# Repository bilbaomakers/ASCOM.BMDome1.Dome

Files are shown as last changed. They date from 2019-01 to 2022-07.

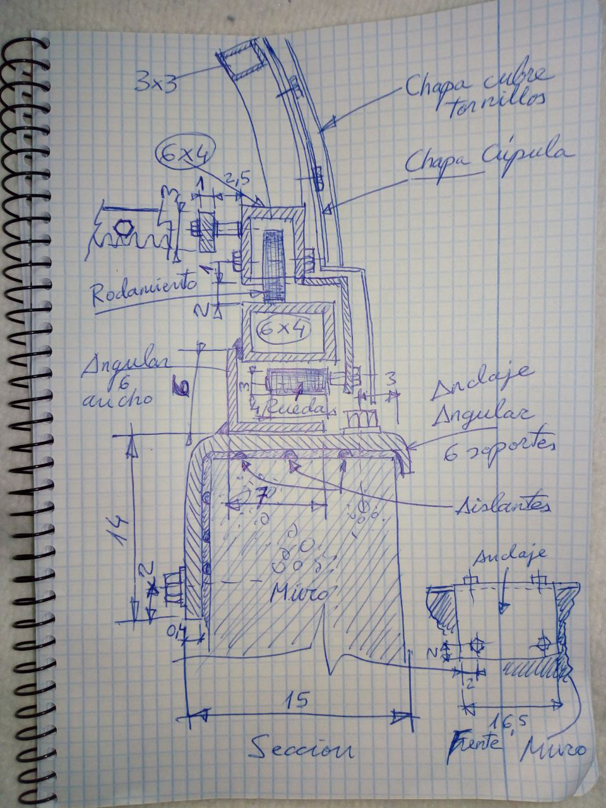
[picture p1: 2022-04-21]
DOCUMENTACION/MECANICA/IMG_20190130_000913_478.jpg

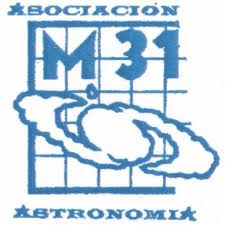
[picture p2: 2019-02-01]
DRIVER ASCOM/ASCOM.BMDome1.Dome/Resources/M31.jpg

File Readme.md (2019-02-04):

# ASCOM DOMO BILBAOMAKERS V 1.0.0

Automatizacion de la cupula del Observatorio Astronomico de Marcilla de Campos (Palencia).

Desarrollado por la comunidad Bilbaomakers: https://bilbaomakers.org/ - info@bilbaomakers.org

Desarrollado bajo licencia GNU GENERAL PUBLIC LICENSE Version 3

Descripcion:

Proyecto para desarrollar un controlador para la orientacion Azimut de la cupula del observatorio y el control de la compuerta (Shutter).

Utiliza Arduino como microcontrolador(es) y MQTT como protocolo de comunicaciones entre el PC y el Hardware

Componentes actuales:

- Driver Ascom - MQTT para el control de la cupula desde el PC (Windows) y/o fuente de tracking ( Software, Scope, ....)
- Codigo para el Hardware (Controlador Arduino para el Azimut y controlador para el Shutter).
- Diseño CAD (freecad) de los elementos mecanicos.

04/02/2019 - Proyecto en Desarrollo V 1.0.0 (Branch Development).

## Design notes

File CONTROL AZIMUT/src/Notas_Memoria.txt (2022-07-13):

NIVEL HARDWARE

Memoria interna del procesador
ROM - 448Kb para boot y core
SRAM - Static RAM - 520Kb
8Kb de SRAM en RTC (Copro)

Memoria externa ROM - SPI Flash (Antigua EEPROM)
W25Q32: 32M-bit / 4M-byte (4,194,304)
Usada habitualmente como memoria de programa, para OTA y sistema de ficheros SPIFFS, a particionar al gusto aunque para arduino en PlatformIO hay una por defecto.

NIVEL SOFTWARE

IROM - Instrucciones en ROM(flash) - Por defecto todas las funciones se almacenan ahi (no necesario modificador en programacion)
DROM - Datos en ROM(flash) - Por defecto todas las constantes se almacenan en la flash (no modificador solo declarar como constante)
D/IRAM - Combinada de las 2 pero no he conseguido saber como definirla.

IRAM_ATTR - Instruction RAM - Instrucciones (funciones) a la RAM (ISR) - void IRAM_ATTR onTimer_stepper(){}
DRAM_ATTR - Data RAM - Datos que se van a manejar desde instrucciones en la IRAM - 

NOTA: Las variables (datos no constantes iniciados en el codigo) se almacenan en la RAM, en los espacios HEAP, STACK o STATICS(volatile). No confundir con la DRAM (espacio para datos de funciones IRAM)

__NOINIT_ATTR - Datos en la Flash que NO se inicializan en restart (permanencen tras rebote).

RTC_NOINIT_ATTR - Datos en la RTC Slow memory (unica memoria accesible por el coprocesador que hay que usar el depp sleep, y accesible despues por los procesadores normales)

DMA_ATTR - Para alojamiento de datos en RAM que utilizan los perifericos DMA (Direct Access Memory). No es obligatorio (se puede poner en el STACK) porque es RAM, pero es mas seguro si hay RAM externa

Tambien hay opcion de RAM externa que no tratamos aqui.

Vista desde el "Scope":
Heap - El computo global de la RAM accesible (en cada tipo, normal, rtc, ...). Es un espacio digamos "dinamico" en funcion de "otros usos" de la RAM.
Stack - Espacio de memoria RAM para cada "Thread". Obviamente no accesible mas que por ese thread. Puede estar localizada a su vez en la RAM normal, en la RTC .....
Estatica - Localizada en HEAP e INAMOVIBLE por el compilador maligno (reservada)

xPortGetFreeHeapSize() - Heap libre (en bytes)

Proceso de arranque:

- First Boot Stage - La CPU0 (CPU_PRO) inicializa el HW y va a su vector 0 (0x40000400)
- Se inicia el second Stage del arranque donde se comprueba las particiones y el contenido de la particion OTA para decidir si cargar ese programa o el "normal"
- Se traslada lo que haya que trasladar de la FLASH a las RAMs y se mapea donde esta todo (De los mapeos se encarga la MMU (Memory Management Unit) que esta entre los procesadores y las memorias)
- En este second stage la CPU1 (APP_CPU) esta parada (logico) y la CPU0 usa su memoria de prestadillo para sus operaciones
- Se salta al vector de inicio de la aplicacion(call_start_cpu0 en ESP_IDF) y se libera la memoria de la CPU_APP la cual sera iniciada por programa nosotros. Hasta aqui el proceso ESP_IDF. Arduino añade mas para el tema setup() loop() ya que inicia el programa "a su forma".

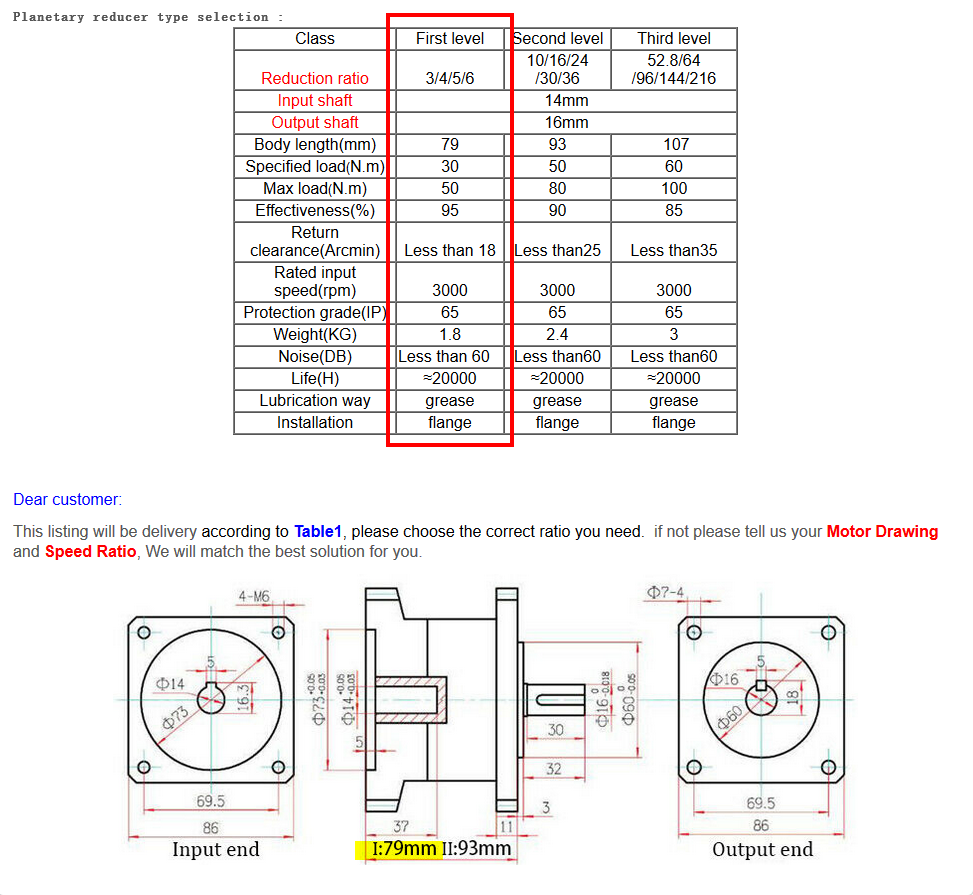
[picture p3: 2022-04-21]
DOCUMENTACION/MECANICA/Reductora.png

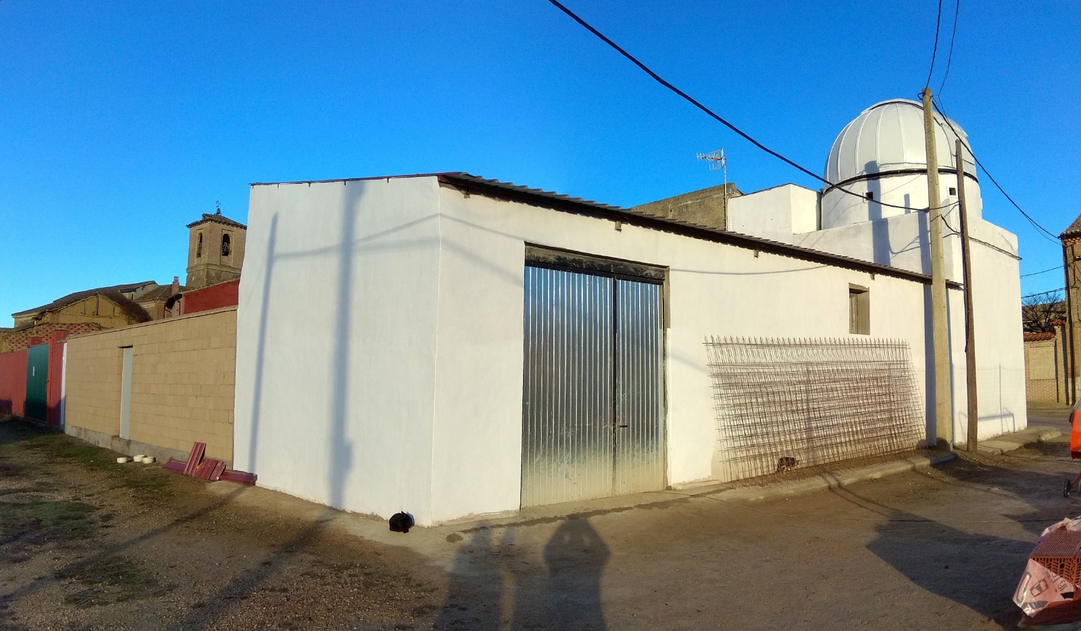
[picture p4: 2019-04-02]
OBSERVATORIO MARCILLA/FOTOS/IMG-20190123-WA0004.jpg

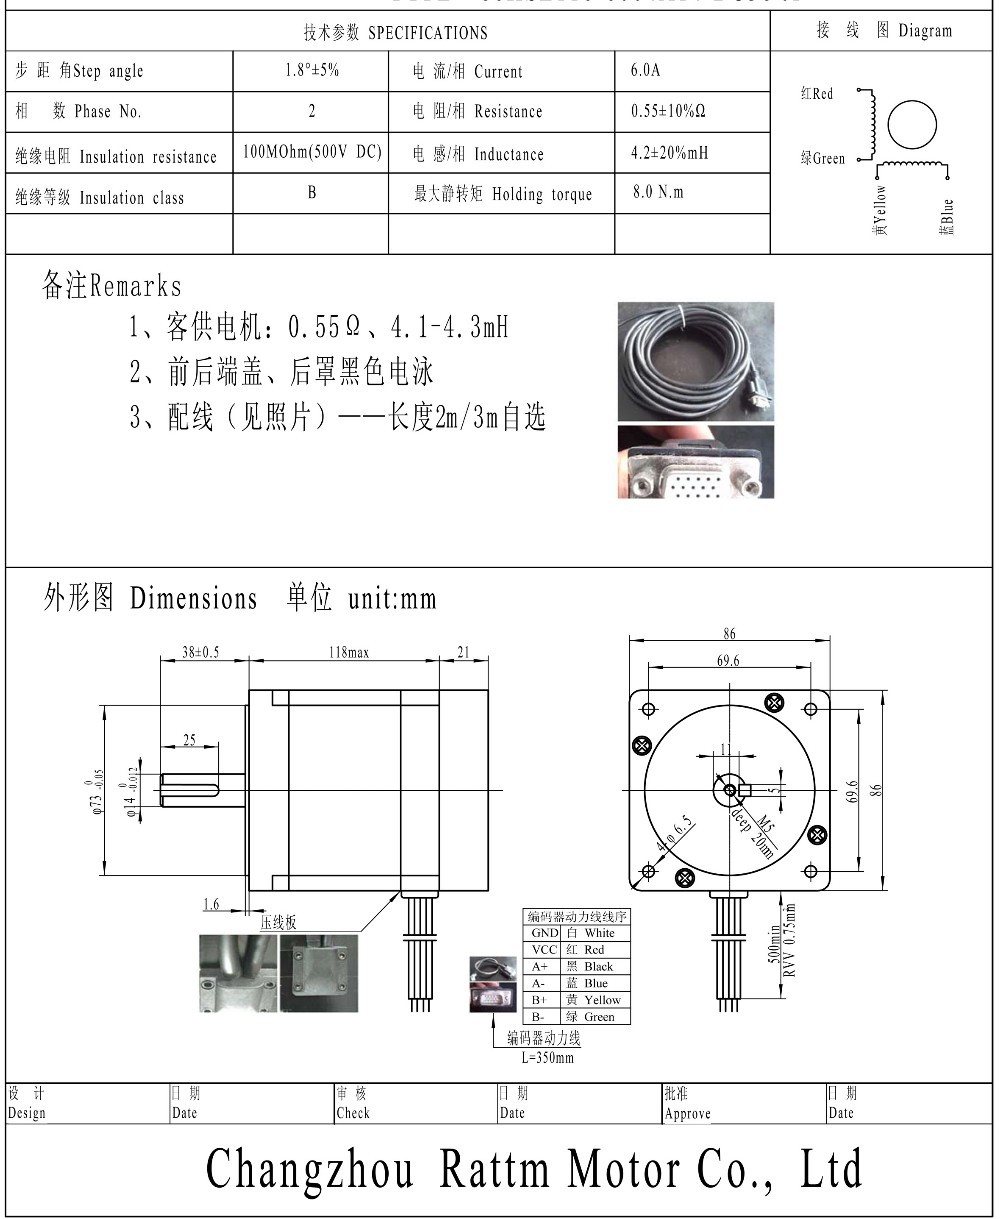
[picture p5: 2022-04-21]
DOCUMENTACION/MECANICA/Stepper_Azimut.jpg

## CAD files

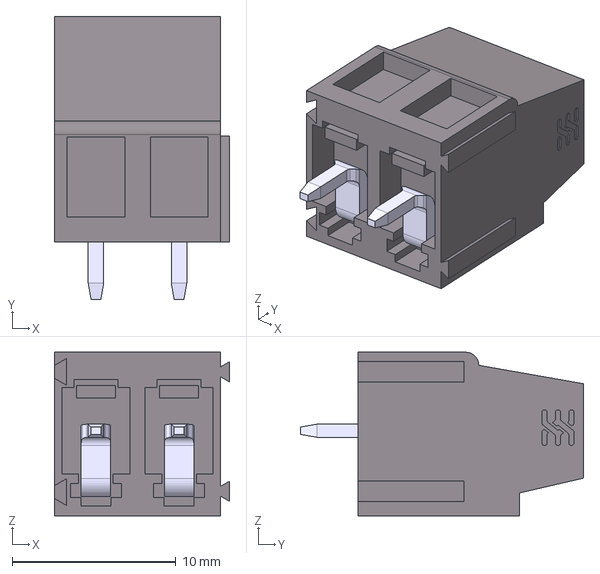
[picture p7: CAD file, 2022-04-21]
CAD/ELECTRONICA/PlacaIOAzimut/PlacaIOAzimut/conector.step.stp
10.7 x 17.3 x 10.0 mm

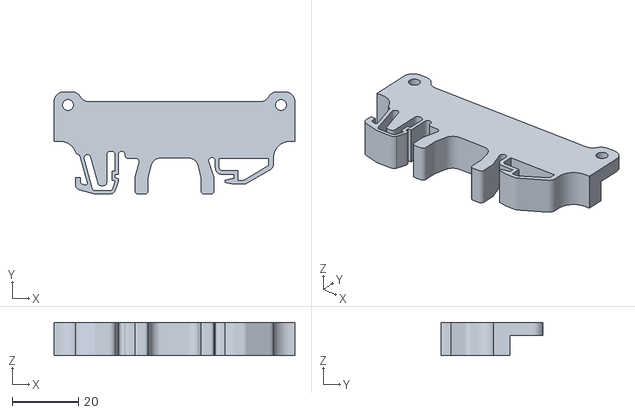
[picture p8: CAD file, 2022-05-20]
CAD/ELECTRONICA/PlacaIOAzimut/PlacaIOAzimut/Placa_Catia/Clip_Din.stl
73.0 x 31.0 x 10.0

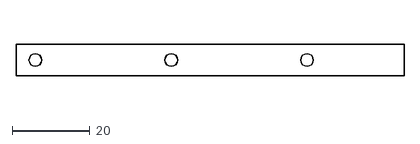
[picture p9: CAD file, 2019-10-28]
CAD/MECANICA/DXF/EXPORTADO FREECAD/Angulo_Fijacion_Taladros_1.dxf
100.0 x 8.00

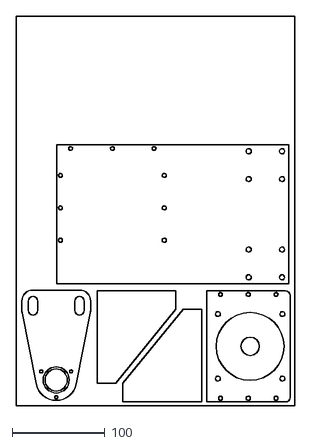
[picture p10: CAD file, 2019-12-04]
CAD/MECANICA/DXF/LIBRECAD/Mecanizado1_exportado_dxf_12.dxf
300.0 x 420.0

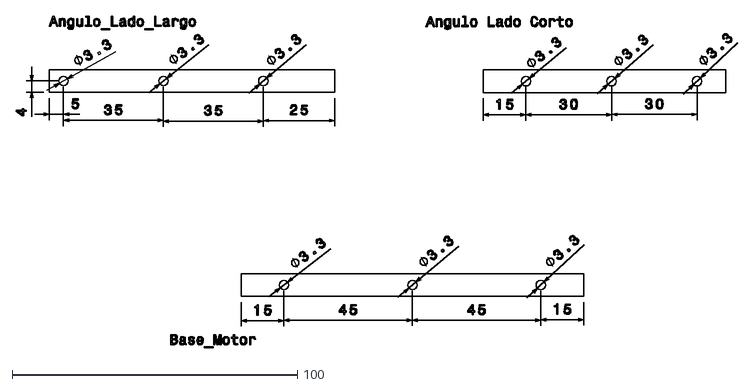
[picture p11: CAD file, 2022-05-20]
CAD/MECANICA/DXF/PLANOS/Taladros_a_mano.dxf
252.8 x 116.3

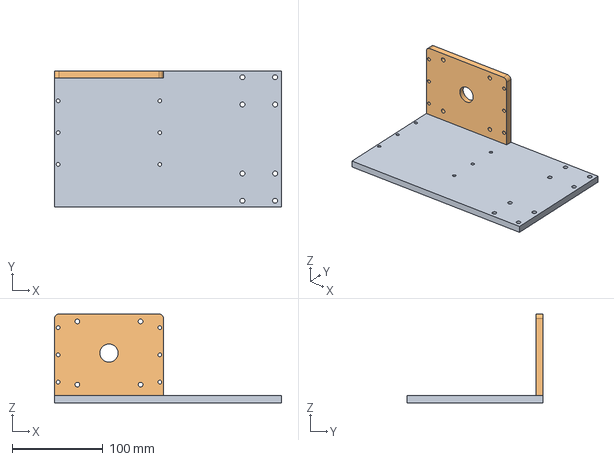
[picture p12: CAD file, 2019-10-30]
CAD/MECANICA/Version_03/A2PLUS/A2Plus_Subconjunto1_Motor.FCStd
250.0 x 150.0 x 98.0 mm
Base_Motor_001
Lateral_Base_Motor_001

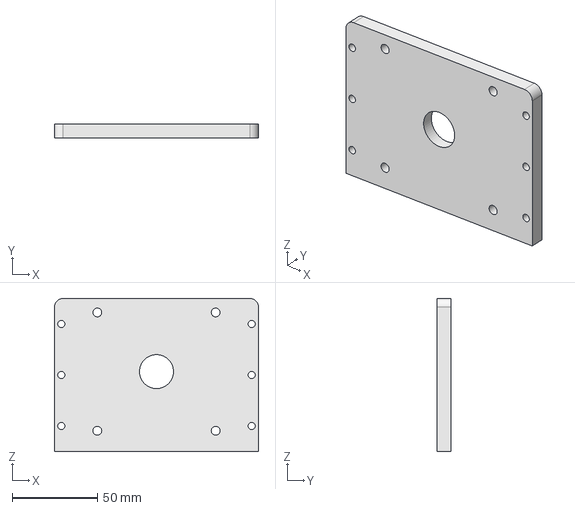
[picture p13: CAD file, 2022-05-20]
CAD/MECANICA/Version_03/CATIA/STEP/Lateral_Base_motor.step
120.0 x 8.00 x 90.0 mm

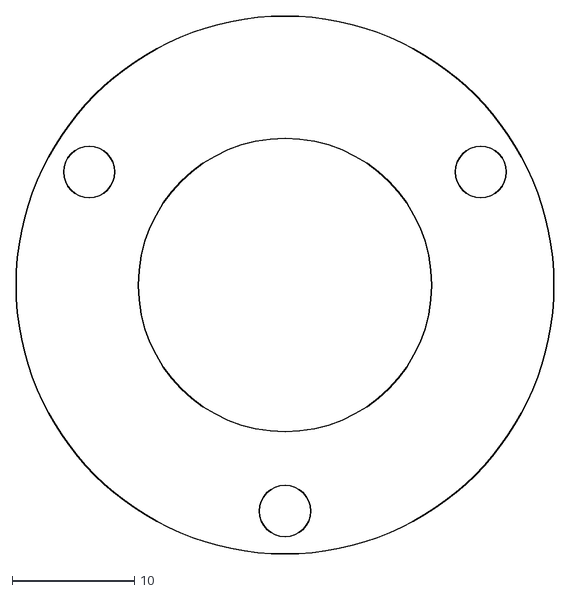
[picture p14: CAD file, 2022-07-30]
CAD/MECANICA/Version_03/CATIA/Tapa_Rodamiento_V2.dxf
44.0 x 44.0

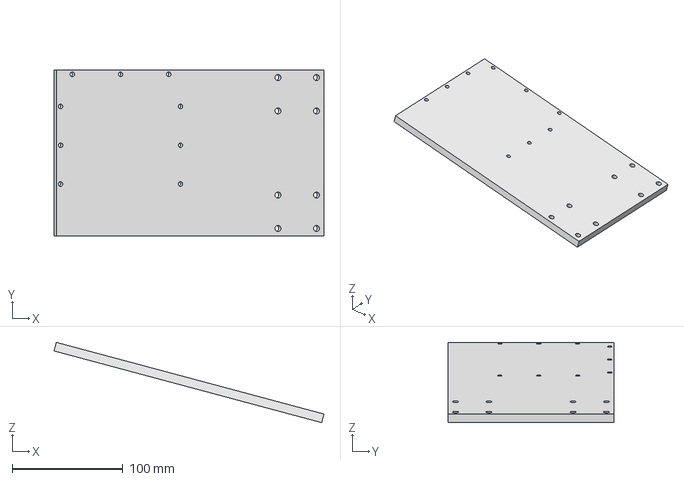
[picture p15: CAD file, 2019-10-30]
CAD/MECANICA/Version_03/OTROS/__Montaje Motor__.FCStd
243.6 x 150.0 x 72.4 mm

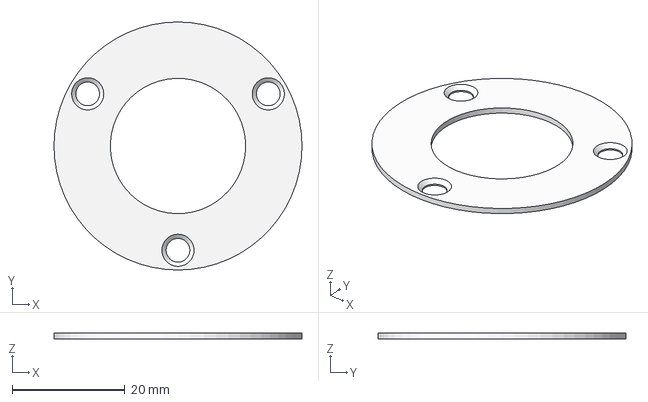
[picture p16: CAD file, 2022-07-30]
CAD/MECANICA/Version_03/PARTS/Tapa_Rodamiento_V2-Body.step
44.0 x 44.0 x 1.00 mm

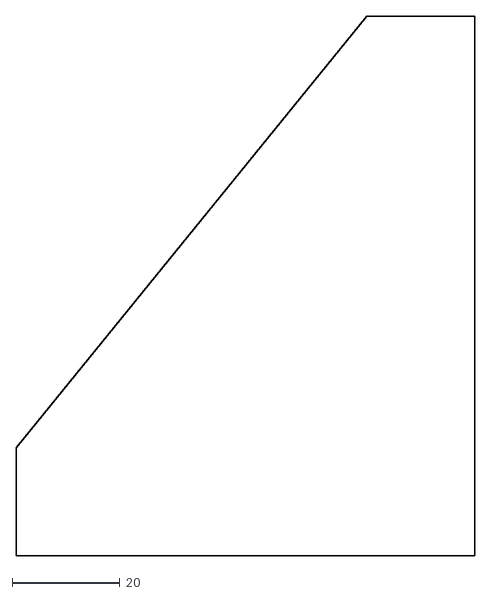
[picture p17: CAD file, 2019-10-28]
CAD/MECANICA/DXF/EXPORTADO FREECAD/Angulo_Fijacion.dxf
85.0 x 100.0

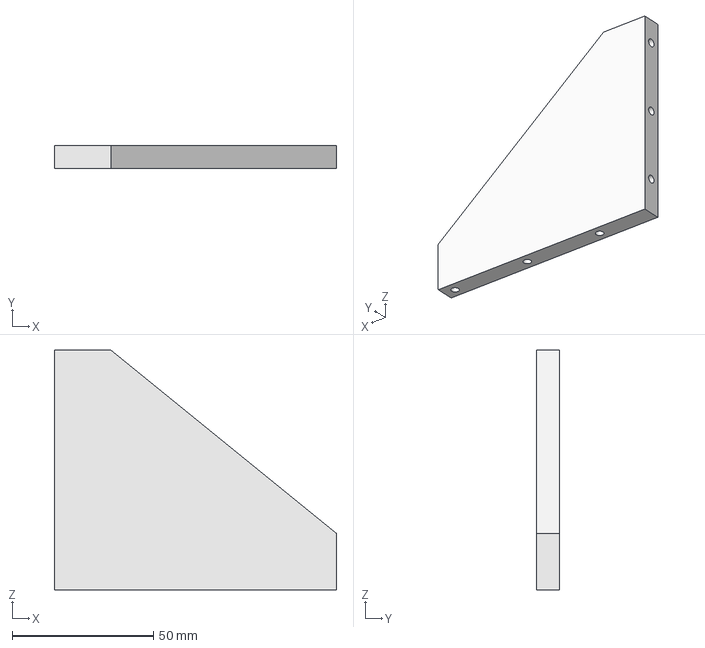
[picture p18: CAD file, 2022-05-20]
CAD/MECANICA/Version_03/CATIA/STEP/Angulo_Fijacion.step
100.0 x 8.00 x 85.0 mm

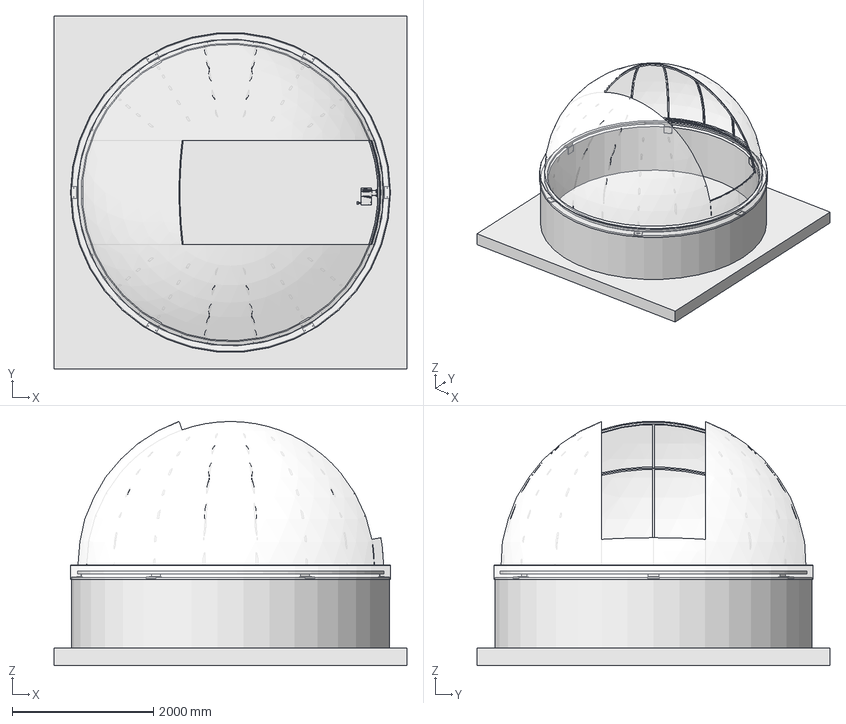
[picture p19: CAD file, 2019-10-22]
CAD/MECANICA/Version_03/OTROS/_MAQUETA_V03.FCStd
5000.0 x 5000.0 x 3461.9 mm
Cupula_Hormigon_001
AroMetalicoSoporteCupulaHormigon_001
Cupula_001
__Montaje Motor___001

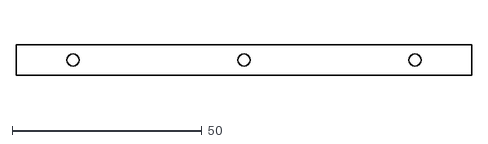
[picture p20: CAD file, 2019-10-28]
CAD/MECANICA/DXF/EXPORTADO FREECAD/Lateral_Base_Motor_taladros1.dxf
120.0 x 8.00

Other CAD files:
CAD/MECANICA/DXF/LIBRECAD/Mecanizado1_exportado.dxf
CAD/MECANICA/Version_03/PARTS/Tapa_Rodamiento_V2.FCStd
CAD/MECANICA/DXF/LIBRECAD/Mecanizado1.dxf
CAD/MECANICA/Version_03/CATIA/STEP/Base_Motor.step
CAD/ELECTRONICA/PlacaIOAzimut/PlacaIOAzimut/Placa_Catia/Clip_Din.CATPart
CAD/ELECTRONICA/PlacaIOAzimut/PlacaIOAzimut/Placa_Catia/PlacaIOAzimut PCB.CATPart
CAD/ELECTRONICA/PlacaIOAzimut/PlacaIOAzimut/Placa_Catia/PlacaIOAzimut.CATProduct
CAD/MECANICA/DXF/EXPORTADO FREECAD/Angulo_Fijacion_Taladros_2.dxf
CAD/MECANICA/DXF/EXPORTADO FREECAD/Angulo_Fijacion_taladros_cara1.dxf
CAD/MECANICA/DXF/EXPORTADO FREECAD/Angulo_Fijacion_taladros_cara2.dxf
CAD/MECANICA/DXF/EXPORTADO FREECAD/Base_Motor.dxf
CAD/MECANICA/DXF/EXPORTADO FREECAD/Lateral_Base_Motor.dxf
CAD/MECANICA/DXF/EXPORTADO FREECAD/Soporte_rodillos.dxf
CAD/MECANICA/DXF/LIBRECAD/OLD/Mecanizado1.dxf
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

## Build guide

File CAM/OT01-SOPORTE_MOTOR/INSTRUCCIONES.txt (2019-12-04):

1.- Planear la mesa con fresa de 6mm pasada 90%. Velocidad 2000. Programa hace una pasada de 1mm. Repetir bajando Z si hace falta

2.- Mecanizados: Fresa 3mm pasada 70%. Cero Z arriba clavado para los vaciados. Verificar 0 en vaciados. Cortes pasan 0.3 abajo

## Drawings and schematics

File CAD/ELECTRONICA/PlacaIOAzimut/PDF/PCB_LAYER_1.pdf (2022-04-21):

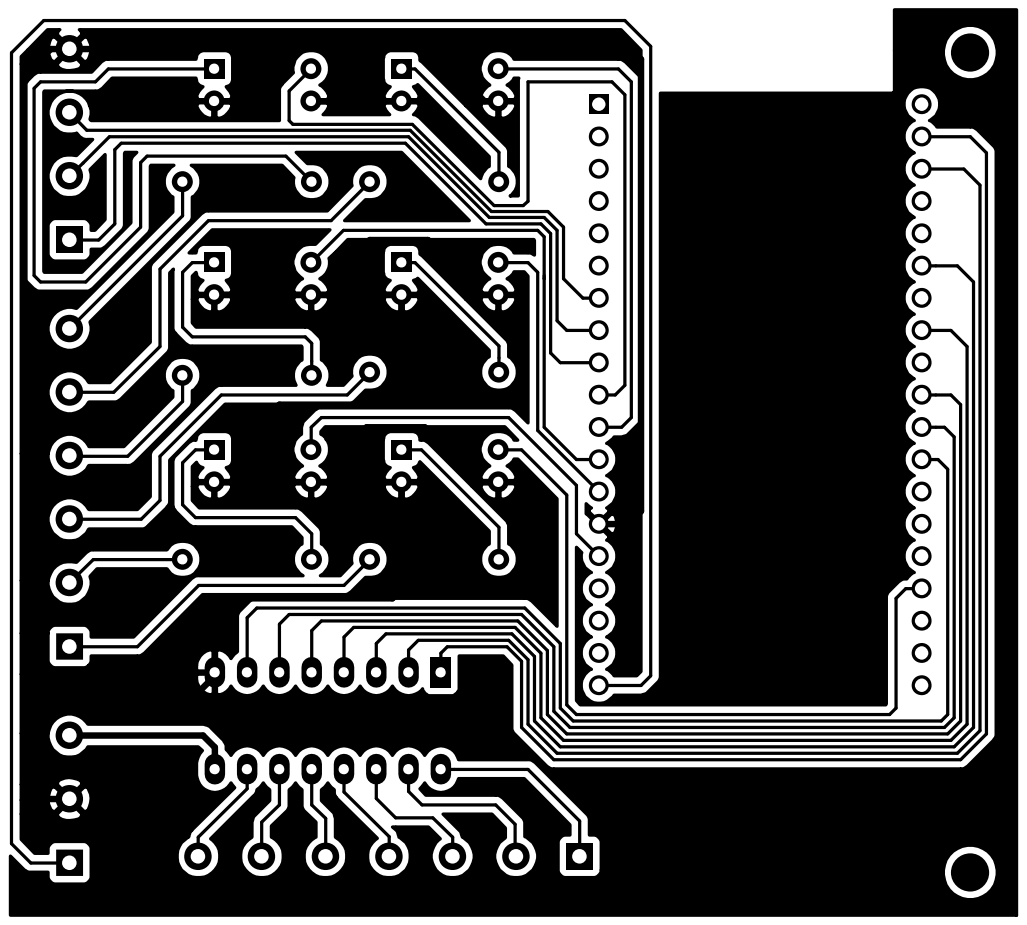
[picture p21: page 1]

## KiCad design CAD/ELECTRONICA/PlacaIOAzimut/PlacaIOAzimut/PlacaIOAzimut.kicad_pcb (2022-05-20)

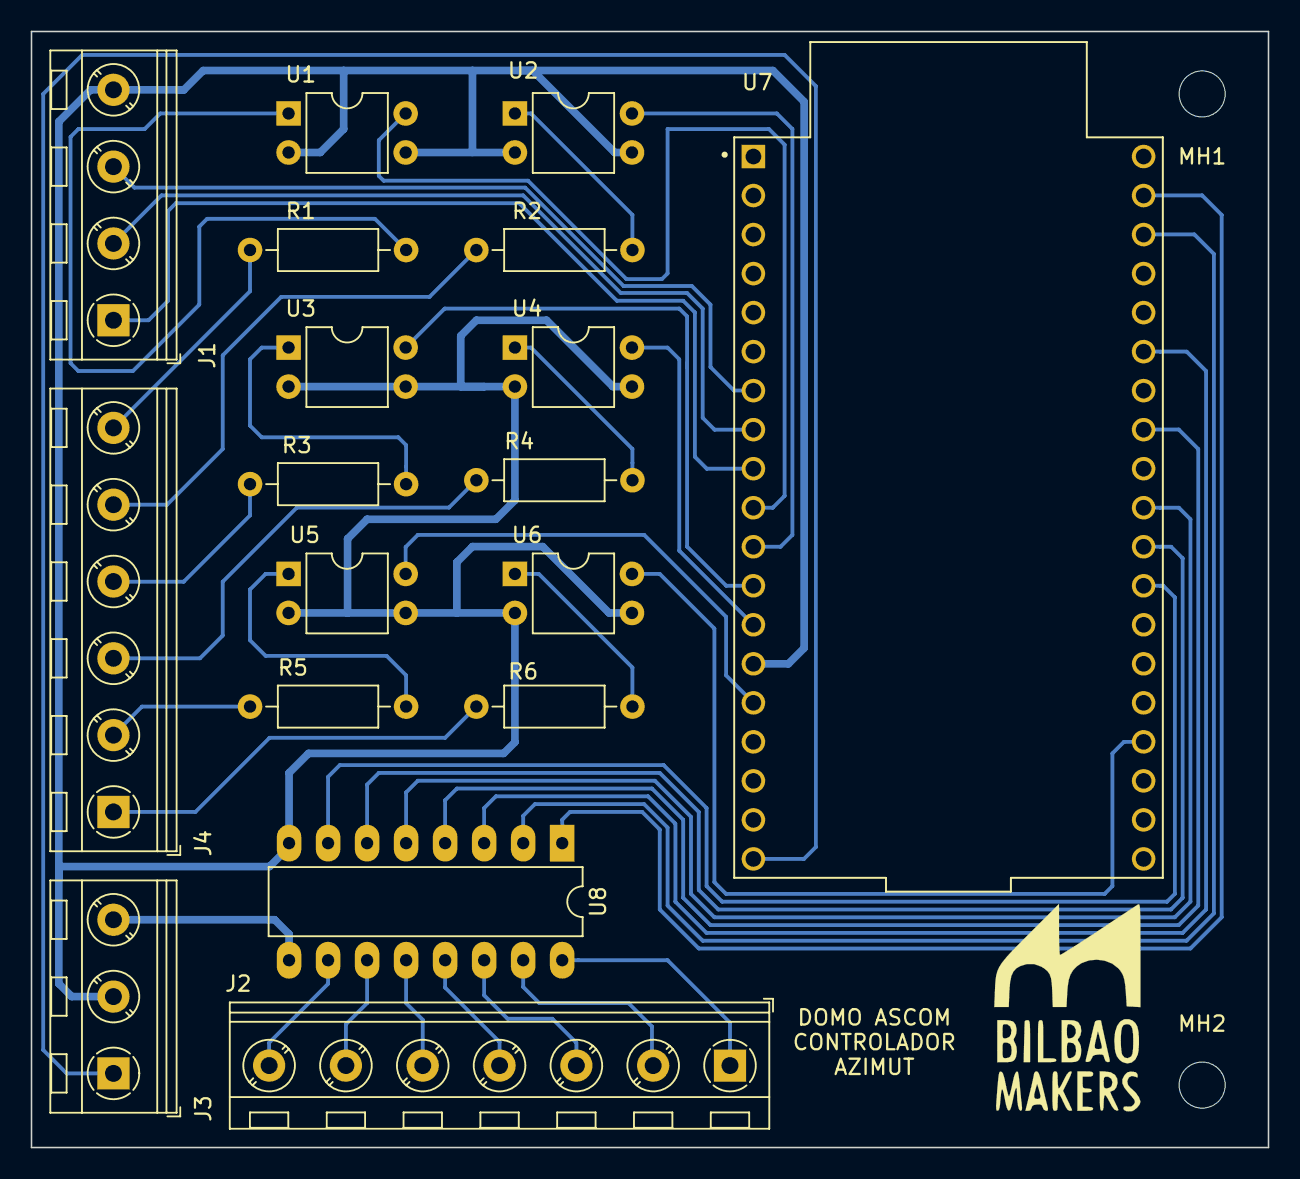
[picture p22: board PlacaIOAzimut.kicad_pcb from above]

Board: 2 copper layers, 80.5 x 72.6 mm, 20 parts (0 on the bottom side), 38 nets.

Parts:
J1: STEPPER DRV; TerminalBlock_RND_205-00047_1x04_P5.00mm_Horizontal
J2: SALIDAS; TerminalBlock_RND_205-00050_1x07_P5.00mm_Horizontal
J3: POWER SUPP; TerminalBlock_RND_205-00046_1x03_P5.00mm_Horizontal
J4: INPUTS; TerminalBlock_RND_205-00049_1x06_P5.00mm_Horizontal
MH1, MH2: 3mm; MountingHole_3mm
R1, R2, R3, R4, R5, R6: 1K; R_Axial_DIN0207_L6.3mm_D2.5mm_P10.16mm_Horizontal
U1, U2, U3, U4, U5, U6: PC817; DIP-4_W7.62mm
U7: ESP32-DEVKITC; MODULE_ESP32-DEVKITC
U8: ULN2003; DIP-16_W7.62mm_LongPads

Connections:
+5V: J3.1, U7.19
+12V: J3.3, U8.9
GND: J1.4, J3.2, U1.2, U1.3, U2.2, U2.3, U3.2, U3.3, U4.2, U4.3, U5.2, U5.3, U6.2, U6.3, U7.14, U8.8
unnamed: J1.1, U7.9
unnamed: J1.2, U7.8
unnamed: J1.3, U7.7
unnamed: J2.1, U8.16
unnamed: J2.2, U8.15
unnamed: J2.3, U8.14
unnamed: J2.4, U8.13
unnamed: J2.5, U8.12
unnamed: J2.6, U8.11
unnamed: J2.7, U8.10
unnamed: J4.1, R6.2
unnamed: J4.2, R5.2
unnamed: J4.3, R4.2
unnamed: J4.4, R3.2
unnamed: J4.5, R2.2
unnamed: J4.6, R1.2
unnamed: R1.1, U1.1
unnamed: R2.1, U2.1
unnamed: R3.1, U3.1
unnamed: R4.1, U4.1
unnamed: R5.1, U5.1
unnamed: R6.1, U6.1
unnamed: U1.4, U7.10
unnamed: U2.4, U7.11
unnamed: U3.4, U7.12
unnamed: U4.4, U7.13
unnamed: U5.4, U7.15
unnamed: U6.4, U7.23
unnamed: U7.27, U8.7
unnamed: U7.28, U8.6
unnamed: U7.29, U8.5
unnamed: U7.31, U8.4
unnamed: U7.33, U8.3
unnamed: U7.36, U8.2
unnamed: U7.37, U8.1

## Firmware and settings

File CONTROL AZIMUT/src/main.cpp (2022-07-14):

 
#pragma region COMENTARIOS

/*

Controlador ASCOM para BMDome1
Description: Driver para controlador de Domo desarrollado por Bilbaomakers
			 para el proyecto de observatorio astronomico en Marcilla de Campos.
			 Control de azimut de la cupula y apertura cierre del shutter.
			 Hardware de control con Arduino y ESP8266
			 Comunicaciones mediante MQTT
Implements:	 ASCOM Dome interface version: 6.4SP1
Author:		 Diego Maroto - BilbaoMakers 2019 - info@bilbaomakers.org



Cosas a hacer en el futuro

- Implementar uno a varios Led WS2812 para informar del estado de lo importante
- Implementar calculo de rotacion basado en mi posicion para "predecir" el movimiento del objeto y poder hacer seguimiento auntonomo automatico
				
Cosas de configuracion a pasar desde el Driver

		- El Azimut cuando esta en HOME
		- El Azimut del PARK


NOTAS SOBRE EL STEPPER Y LA LIBRERIA ACCELSTEPPER

- El ancho minimo de pulso que puede generar la libreria es 20uS, por tanto el periodo minimo es 40uS - Frecuencia Maxima 25Khz
- Una velocidad de motor aceptable inicialmente son 50 revoluciones por minuto (50 tiene el motor de puerta corredera actual pero como soy un maniatico me gusta mas 60)
- Eso es 1 vuelta por segundo en la reductora, que como es 1:6 son 6 revoluciones / segundo del motor
- A 3200 pulsos por vuelta en la controladora, para 6 rev/segundo son 19200 pulsos por segundo. Es el maximo que puedo exprimir la libreria.
- Determinaremos la velocidad optima de la cupula "in situ", originalmente probaremos mas lento cuando montemos.

- Para ejecutar el comando "run" de la libreria Accelstepper vamos a usar la interrupcion de un timer.
- ESP32 tiene 4 timers que funcionan a una frecuencia de 80 MHz (Ole!). Nos sobra "velocidad" que te cagas aqui
- No tengo ni idea de cuantos ciclos de reloj usa el run() de la libreria (lo investigare a ver)

################################################################################

Funcionalidades del cuadro de usuario.

LUZ ROJA - Avisos
	ERROR - 3 pulsos largos (seta apretada al armar, mover sin armar, .....)
	Aviso AbortSlew - 2 pulsos medios
	Aviso buscando casa - 1 pulso largo
	Aviso al terminar de iniciar el sistema - 3 pulsos cortos rapidos
	Aviso botones - Click 1 pulso corto - Hold 2 pulsos cortos

LUZ VERDE - Comunicaciones
	Conectando a la wifi - 1 pulso por segundo
	Conectando al MQTT - 2 pulsos cortos y 1 segundo idle
	Comunicaciones OK - Permanente

LUZ AZUL - ESTADO DEL 
	HW NOT INIT - Apaga
	HW OK READY - Encendido
	SLEWING - 1 pulso por segundo

BOTON1 - AZUL
	CLICK - Inicializa Hardware STD (busca home)
	HOLD - Inicializa Hardware FORCE (sin buscar home)
	
BOTON2 - VERDE
	CLICK - Mover a 90 (SlewToAZimut)
	HOLD - Set Park en la posicion actual (SetParkHere)
	
BOTON3 - ROJO
	CLICK - Parada Normal (AbortSlew)
	HOLD - Aparcar (Park)

BOTON4 - VERDE
	CLICK - Mover a 270 (SlewToAZimut)
	HOLD - 

*/

#pragma endregion

#pragma region INCLUDES
// Librerias comantadas en proceso de sustitucion por la WiFiMQTTManager

#include <AsyncMqttClient.h>			// Vamos a probar esta que es Asincrona: https://github.com/marvinroger/async-mqtt-client
#include <AccelStepper.h>				// Para controlar el stepper como se merece: https://www.airspayce.com/mikem/arduino/AccelStepper/classAccelStepper.html
#include <FS.h>							// Libreria Sistema de Ficheros
#include <WiFi.h>						// Para las comunicaciones WIFI del ESP32
#include <DNSServer.h>					// La necesita WifiManager para el portal captivo
#include <WebServer.h>					// La necesita WifiManager para el formulario de configuracion (ESP32)
#include <ArduinoJson.h>				// OJO: Tener instalada una version NO BETA (a dia de hoy la estable es la 5.13.4). Alguna pata han metido en la 6
#include <string>						// Para el manejo de cadenas
#include <Bounce2.h>					// Libreria para filtrar rebotes de los Switches: https://github.com/thomasfredericks/Bounce2
#include <SPIFFS.h>						// Libreria para sistema de ficheros SPIFFS
#include <NTPClient.h>					// Para la gestion de la hora por NTP
#include <WiFiUdp.h>					// Para la conexion UDP con los servidores de hora.
#include <OneButton.h> 					// Para los botones de usuario: https://github.com/mathertel/OneButton
#include <IndicadorLed.h>				// Mi libreria para Leds

#pragma endregion

#pragma region Constantes y configuracion. Modificable aqui por el usuario

#define CONFIG_TASK_WDT_CHECK_IDLE_TASK_CPU1 0

// Para la configuracion de conjunto Mecanico de arrastre
static const uint8_t MECANICA_STEPPER_PULSEPIN = 25;					// Pin de pulsos del stepper
static const uint8_t MECANICA_STEPPER_DIRPIN = 33;						// Pin de direccion del stepper
static const uint8_t MECANICA_STEPPER_ENABLEPING = 32;				// Pin de enable del stepper
static const short MECANICA_PASOS_POR_VUELTA_MOTOR = 400;		// Numero de pasos por vuelta del STEPPER (Configuracion del controlador)
static const float MECANICA_STEPPER_MAXSPEED = (MECANICA_PASOS_POR_VUELTA_MOTOR * 5);	// Velocidad maxima del stepper (pasos por segundo)
static const float MECANICA_STEPPER_MAXSPEED_INST = (MECANICA_PASOS_POR_VUELTA_MOTOR * 2);	// Velocidad maxima del stepper en modo instalador (pasos por segundo)
static const float MECANICA_STEPPER_MAXACELERATION = (MECANICA_STEPPER_MAXSPEED / 3);	// Aceleracion maxima del stepper (pasos por segundo2). Aceleraremos al VMAX en 3 vueltas del motor.
static const float MECANICA_STEPPER_MAXACELERATION_INST = (MECANICA_STEPPER_MAXSPEED_INST / 3);	// Aceleracion maxima del stepper modo instalador(pasos por segundo2). Aceleraremos al VMAX en 3 vueltas del motor.
static const short MECANICA_RATIO_REDUCTORA = 6;							// Ratio de reduccion de la reductora
static const short MECANICA_DIENTES_PINON_ATAQUE = 16;				// Numero de dientes del piños de ataque
static const short MECANICA_DIENTES_CREMALLERA_CUPULA = 981;	// Numero de dientes de la cremallera de la cupula
static const boolean MECANICA_STEPPER_INVERTPINS = false;			// Invertir la logica de los pines de control (pulso 1 o pulso 0)
static const int MECANICA_STEPPER_ANCHO_PULSO = 10;						// Ancho de los pulsos

// Entradas
static const uint8_t MECANICA_BOTONPANEL1 = 15;
static const uint8_t MECANICA_BOTONPANEL2 = 13;
static const uint8_t MECANICA_BOTONPANEL3 = 12;
static const uint8_t MECANICA_BOTONPANEL4 = 14;
static const uint8_t MECANICA_EMERGENCY_STOP = 27;
static const uint8_t MECANICA_SENSOR_HOME = 26;								// Pin para el sensor de HOME

// Salidas
static const uint8_t MECANICA_LEDROJO = 16;
static const uint8_t MECANICA_LEDVERDE = 17;
static const uint8_t MECANICA_LEDAZUL = 5;
static const uint8_t MECANICA_SALIDA4 = 19;
static const uint8_t MECANICA_SALIDA5 = 21;
static const uint8_t MECANICA_SALIDA6 = 22;
static const uint8_t MECANICA_SALIDA7 = 23;

// Para el ticker del BMDomo1
unsigned long TIEMPO_TICKER_RAPIDO = 500;

// Para la zona horaria (horas de diferencia con UTC)
static const int HORA_LOCAL = 2;

// PARA MODO INSTALADOR. Para que la cupula tenga la funcionalidad reducida lo justo para el instalador
static const boolean MODO_INSTALADOR = true;


#pragma endregion

#pragma region DEFINICIONES

enum TipoEstadoMecanica{

	MEC_NOT_INIT,
	MEC_INITIALIZING,
	MEC_OK,
	MEC_EMERGENCY,

}estadoMecanica;

enum TipoEstadoMovimiento {

	MOV_BUSCANDOCASA,
	MOV_APARCANDO,
	MOV_OKSTOPPED,
	MOV_OKSLEWING,
	MOV_ERROR,

}estadoMovimiento;

enum TipoEstadoComunicaciones {

	COM_OK,

}estadoComunicaciones;


// VARIABLES
//bool Inicializando;							// Para saber que estamos ejecutando el comando INITHW
//bool BuscandoCasa;							// Para saber que estamos ejecutando el comando FINDHOME
//bool Aparcando;								// Para saber si estamos yendo a aparcar
float TotalPasos;							// Variable para almacenar al numero de pasos totales para 360º (0) al iniciar el objeto.
bool HayQueSalvar;							// 
String HardwareInfo;						// Identificador del HardWare y Software
bool ComOK;									// Si la wifi y la conexion MQTT esta OK
bool DriverOK;								// Si estamos conectados al driver del PC y esta OK
//bool HardwareOK;							// Si nosotros estamos listos para todo (para informar al driver del PC)
//bool Slewing;								// Si alguna parte del Domo esta moviendose
bool AtHome;								// Si esta parada en HOME
bool AtPark;								// Si esta en la posicion de PARK									
int ParkPos;								// Para almacenar la posicion de Park en la clase
//bool emergencyStop;							// Para almacenar el estado de la seta de emergencia
// Para el sensor de temperatura de la CPU. Definir aqui asi necesario es por no estar en core Arduino.
extern "C" {uint8_t temprature_sens_read();}

// FUNCIONES
String MiEstadoJson(int categoria);			// Devuelve un JSON con los estados en un array de 100 chars (la libreria MQTT no puede con mas de 100)
void MoveTo(int azimut);					// Mover la cupula a un azimut
void IniciaCupula(String parametros);		// Inicializar la cupula
void ApagaCupula(String parametros);		// Apagar la cupula normalmente.
void FindHome();							// Mueve la cupula a Home
long GetCurrentAzimut();					// Devuelve el azimut actual de la cupula
void Run();									// Actualiza las propiedades de estado de este objeto en funcion del estado de motores y sensores
void Connected();							// Para implementar la propiedad-metodo Connected
void Connected(boolean status);				// Para implementar la propiedad-metodo Connected
void AbortSlew();
void SetPark(int l_ParkPos);
void Park();
boolean LeeConfig();
void MandaRespuesta(String comando, String payload);		
long GradosToPasos(long grados);			// Convierte Grados a Pasos segun la mecanica
long PasosToGrados(long pasos);		  		// Convierte pasos a grados segun la mecanica
boolean SalvaConfig();
void EmergencyStop();						// Parada de emergencia de la cupula

// OBJETOS
Bounce Debouncer_HomeSwitch = Bounce(); 	// Objeto debouncer para el switch HOME
Bounce Debouncer_Emergency_Stop = Bounce(); 	// Objeto debouncer para la seta de emergencia

// Para la conexion MQTT
AsyncMqttClient  clienteMqtt;

// Controlador Stepper
AccelStepper controladorStepper;

// Los manejadores para las tareas. El resto de las cosas que hace nuestro controlador que son un poco mas flexibles que la de los pulsos del Stepper
TaskHandle_t tHandleTaskCupulaRun,tHandleTaskProcesaComandos,tHandleTaskComandosSerieRun,tHandleTaskMandaTelemetria,tHandleTaskGestionRed,tHandleTaskEnviaRespuestas, tHandleTaskGestionCuadro;	

// Manejadores Colas para comunicaciones inter-tareas
QueueHandle_t colaComandos,colaRespuestas;

// Timer Stepper Run
hw_timer_t * timer_stp = NULL;
portMUX_TYPE timerMux = portMUX_INITIALIZER_UNLOCKED;

// Flag para el estado del sistema de ficheros
boolean spiffStatus = false;

// Conexion UDP para la hora
WiFiUDP udpNtp;

// Manejador del NTP. Cliente red, servidor, offset zona horaria, intervalo de actualizacion.
// FALTA IMPLEMENTAR ALGO PARA CONFIGURAR LA ZONA HORARIA
NTPClient clienteNTP(udpNtp, "europe.pool.ntp.org", HORA_LOCAL * 3600, 3600);

// Cuado Mando
IndicadorLed ledRojo (MECANICA_LEDROJO, false);
IndicadorLed ledVerde (MECANICA_LEDVERDE, false);
IndicadorLed ledAzul (MECANICA_LEDAZUL, false);
OneButton boton1 (MECANICA_BOTONPANEL1,true,true);
OneButton boton2 (MECANICA_BOTONPANEL2,true,true);
OneButton boton3 (MECANICA_BOTONPANEL3,true,true);
OneButton boton4 (MECANICA_BOTONPANEL4,true,true);

#pragma endregion

#pragma region CLASE ConfigClass

class ConfigClass{

	private:

		String c_fichero;
	
	public:
	
		char mqttserver[40];
		char mqttport[6];
		char mqtttopic[33];
		char mqttusuario[19];
		char mqttpassword[25];

		String cmndTopic;
		String statTopic;
		String teleTopic;
		String lwtTopic;

		// Esto no se salva en el fichero, lo hace el objeto Wifi
		// Lo pongo aqui como almacenamiento temporal para los comandos de configuracion
		char Wssid[30];
		char WPasswd[100];


		// Otras configuraciones permanentes del la cupula
		int ParkPos;

		ConfigClass(String fichero);
		~ConfigClass() {};

		boolean leeconfig ();
		boolean escribeconfig ();
		
};

	// Constructor
	ConfigClass::ConfigClass(String fichero){

		c_fichero = fichero;

		//leeconfig();

		mqttserver[0]= '\0';
		mqttport[0] = '\0';
		mqtttopic[0] = '\0';
		mqttusuario[0] = '\0';
		mqttpassword[0] = '\0';

		Wssid[0] = '\0';
		WPasswd[0]  = '\0';	
				
	}

	// Seer la configuracion desde el fichero
	boolean ConfigClass::leeconfig(){
	
		if (SPIFFS.exists(c_fichero)) {
			// Si existe el fichero abrir y leer la configuracion y asignarsela a las variables definidas arriba
			File ComConfigFile = SPIFFS.open(c_fichero, "r");
			if (ComConfigFile) {
				size_t size = ComConfigFile.size();
				// Declarar un buffer para almacenar el contenido del fichero
				std::unique_ptr<char[]> buf(new char[size]);
				// Leer el fichero al buffer
				ComConfigFile.readBytes(buf.get(), size);
				DynamicJsonBuffer jsonBuffer;
				JsonObject& json = jsonBuffer.parseObject(buf.get());
				//json.printTo(Serial);
				
				if (json.success()) {
					Serial.print("Configuracion del fichero leida: ");
					json.printTo(Serial);
				    Serial.println("");

					// Leer los valores del MQTT
					strcpy(mqttserver, json["mqttserver"]);
					strcpy(mqttport, json["mqttport"]);
					strcpy(mqtttopic, json["mqtttopic"]);
					strcpy(mqttusuario, json["mqttusuario"]);
					strcpy(mqttpassword, json["mqttpassword"]);

					// Dar valor a las strings con los nombres de la estructura de los topics
					cmndTopic = "cmnd/" + String(mqtttopic) + "/#";
					statTopic = "stat/" + String(mqtttopic);
					teleTopic = "tele/" + String(mqtttopic);
					lwtTopic = teleTopic + "/LWT";
					return true;

					Serial.println("Servidor MQTT: " + String(mqttserver)) + ":" + String(mqttport);
					Serial.println("Topic Comandos: " + cmndTopic);
					Serial.println("Topic Respuestas: " + statTopic);
					Serial.println("Topic Telemetria: " + teleTopic);
					Serial.println("Topic LWT: " + lwtTopic);
										
				}
					
				else {

					Serial.println("No se puede cargar la configuracion desde el fichero");
					return false;

				}
			}

			else {

				Serial.println ("No se puede leer el fichero de configuracion");
				return false;

			}

		}

		else	{

				Serial.println("No se ha encontrado un fichero de configuracion.");
				Serial.println("Por favor configura el dispositivo desde el terminal serie y reinicia el controlador.");
				return false;

		}

	}
	
	// Salvar la configuracion en el fichero
	boolean ConfigClass::escribeconfig(){

		Serial.println("Salvando la configuracion en el fichero");
		DynamicJsonBuffer jsonBuffer;
		JsonObject& json = jsonBuffer.createObject();
		json["mqttserver"] = mqttserver;
		json["mqttport"] = mqttport;
		json["mqtttopic"] = mqtttopic;
		json["mqttusuario"] = mqttusuario;
		json["mqttpassword"] = mqttpassword;
		
		File ComConfigFile = SPIFFS.open(c_fichero, "w");
		if (!ComConfigFile) {
			Serial.println("No se puede abrir el fichero de configuracion de las comunicaciones");
			return false;
		}

		//json.prettyPrintTo(Serial);
		json.printTo(ComConfigFile);
		ComConfigFile.close();
		Serial.println("Configuracion Salvada");
		
		// Dar valor a las strings con los nombres de la estructura de los topics
		cmndTopic = "cmnd/" + String(mqtttopic) + "/#";
		statTopic = "stat/" + String(mqtttopic);
		teleTopic = "tele/" + String(mqtttopic);
		lwtTopic = teleTopic + "/LWT";

		return true;

	}

	// Objeto de la clase ConfigClass (configuracion guardada en el fichero)
	ConfigClass MiConfig = ConfigClass("/Comunicaciones.json");

#pragma endregion

#pragma region Funciones Cupula

// Para Inicializar variables y demas.
void InitObjCupula() {	

	HardwareInfo = "BMDome1.HWAz.1.0";
	//Inicializando = false;
	ComOK = false;
	DriverOK = false;
	//HardwareOK = false;
	//Slewing = false;			
	//BuscandoCasa = false;
	AtHome = false;
	AtPark = false;
	//Aparcando = false;

	estadoMecanica=MEC_NOT_INIT;
	estadoMovimiento=MOV_ERROR;

	TotalPasos = (float)(MECANICA_DIENTES_CREMALLERA_CUPULA * MECANICA_RATIO_REDUCTORA * MECANICA_PASOS_POR_VUELTA_MOTOR) / (float)(MECANICA_DIENTES_PINON_ATAQUE);
	// Inicializacion del sensor de HOME
	pinMode(MECANICA_SENSOR_HOME, INPUT_PULLUP);
	Debouncer_HomeSwitch.attach(MECANICA_SENSOR_HOME);
	Debouncer_HomeSwitch.interval(30);
	// Inicializacion del sensor Seta Emergencia
	pinMode(MECANICA_EMERGENCY_STOP, INPUT_PULLUP);
	Debouncer_Emergency_Stop.attach(MECANICA_EMERGENCY_STOP);
	Debouncer_Emergency_Stop.interval(5);

	ParkPos = 0;
	HayQueSalvar = false;

}

// Traduce Grados a Pasos segun la mecanica
long GradosToPasos(long grados) {

	return round((float)(grados * TotalPasos) / 360);
	
}

// Traduce Pasos a Grados segun la mecanica
long PasosToGrados(long pasos) {

	// Con una pequeña correccion porque a veces si se pide la posicion por encima de 359.5 devuelve 360 (por el redondeo) y no vale, tiene que ser 0
	long t_grados = round((float)(pasos * 360) / (float)TotalPasos);
	
	if (t_grados == 360) {

		return 0;

	}
		
	else {

		return t_grados;

	}
}

// Metodo que devuelve un JSON con el estado
String MiEstadoJson(int categoria) {

	DynamicJsonBuffer jBuffer;
	JsonObject& jObj = jBuffer.createObject();

	// Dependiendo del numero de categoria en la llamada devolver unas cosas u otras
	switch (categoria)
	{

	case 1:

		// Esto llena de objetos de tipo "pareja propiedad valor"
		jObj.set("TIME", clienteNTP.getFormattedTime());							// HORA
		jObj.set("HI", HardwareInfo);												// Info del Hardware
		jObj.set("CS", ComOK);														// Info de la conexion WIFI y MQTT
		jObj.set("DS", DriverOK);													// Info de la comunicacion con el DRIVER ASCOM (o quiza la cambiemos para comunicacion con "cualquier" driver, incluido uno nuestro
		jObj.set("HS", HardwareOK);													// Info del estado de inicializacion de la mecanica
		jObj.set("AZ", GetCurrentAzimut());											// Posicion Actual (AZ)
		jObj.set("ATH", AtHome); 													// Propiedad AtHome
		jObj.set("PRK", ParkPos);													// Posicion almacenada de Park
		jObj.set("ATPRK", AtPark);													// Propiedad AtPark
		jObj.set("POS", controladorStepper.currentPosition());  					// Posicion en pasos del objeto del Stepper
		jObj.set("TOT", TotalPasos);												// Numero total de pasos por giro de la cupula
		jObj.set("MAXT", controladorStepper.maxexectime());							// Tiempo de ejecucion maxima del ciclo Stepper
		jObj.set("RSSI", WiFi.RSSI());												// RSSI de la señal Wifi
		jObj.set("HALL", hallRead());												// Campo magnetico en el MicroProcesador
		jObj.set("ITEMP", (int)(temprature_sens_read() - 32) / 1.8);				// Temperatura de la CPU convertida a Celsius.

		break;

	case 2:

		jObj.set("INFO2", "INFO2");							
		
		break;

	default:

		jObj.set("NOINFO", "NOINFO");						// MAL LLAMADO

		break;
	}


	// Crear un buffer (aray de 100 char) donde almacenar la cadena de texto del JSON
	char JSONmessageBuffer[200];

	// Tirar al buffer la cadena de objetos serializada en JSON con la propiedad printTo del objeto de arriba
	jObj.printTo(JSONmessageBuffer, sizeof(JSONmessageBuffer));

	// devolver el char array con el JSON
	return JSONmessageBuffer;
	
}

// Metodos (funciones). TODAS Salvo la RUN() deben ser ASINCRONAS. Jamas se pueden quedar uno esperando. Esperar a lo bobo ESTA PROHIBIDISISISISMO, tenemos MUCHAS cosas que hacer ....
void IniciaCupula(String parametros) {

	switch (estadoMecanica)
	{
	case MEC_EMERGENCY:
		ledRojo.Pulsos(1500,500,3);
		MandaRespuesta("InitHW", "ERR_EMERG");
		break;

	case MEC_OK:
		MandaRespuesta("InitHW", "READY");
		break;

	case MEC_NOT_INIT:

		if (parametros == "FORCE") {

			estadoMecanica=MEC_OK;
			MandaRespuesta("InitHW", "READY");
			controladorStepper.enableOutputs();
			
		}

		else if (parametros == "STD"){


			//Inicializando = true;
			estadoMecanica=MEC_INITIALIZING;

			// Activar el motor. el resto del objeto Stepper ya esta OK
			controladorStepper.enableOutputs();

			// Como el metodo ahora mismo es dar toda la vuelta, hago cero. Si cambio el metodo esto no valdria.
			controladorStepper.setCurrentPosition(0);

			// Busca Home (Asyncrono)
			FindHome();

		}
		break;

	default:
		break;
	}
	
}

// Funcion que da orden de mover la cupula para esperar HOME.
void FindHome() {


	switch (estadoMecanica){

	case MEC_NOT_INIT:
		MandaRespuesta("FindHome", "ERR_HNI");
		ledRojo.Pulsos(1500,500,3);
		break;
		
	case MEC_EMERGENCY:
		MandaRespuesta("FindHome", "ERR_EME");
		ledRojo.Pulsos(1500,500,3);
		break;

	case MEC_INITIALIZING: case MEC_OK:

			switch (estadoMovimiento)
			{
				case MOV_OKSLEWING:
					MandaRespuesta("FindHome", "ERR_SLW");
					ledRojo.Pulsos(1500,500,3);
					break;
				
				case MOV_BUSCANDOCASA:
					MandaRespuesta("FindHome", "ERR_FH");
					ledRojo.Pulsos(1500,500,3);
					break;

				case MOV_APARCANDO:
					MandaRespuesta("FindHome", "ERR_PRK");
					ledRojo.Pulsos(1500,500,3);
					break;

				case MOV_OKSTOPPED:

					if (AtHome) {

						// Caramba ya estamos en Home y Parados No tenemos que hacer nada
						MandaRespuesta("FindHome", "ATHOME");
						break;

					}

					else{

						MandaRespuesta("FindHome", "CMD_OK");

						// Pues aqui si que hay que movernos hasta que encontremos casa y pararnos.
						// Aqui nos movemos (de momento a lo burro a dar media vuelta entera)
						MoveTo(180);

						// Pero tenemos que salir de la funcion esta no podemos estar esperando a que de la vuelta asi que activo el flag para saber que "estoy buscando home" y termino
						estadoMovimiento=MOV_BUSCANDOCASA;

					}
					break;

				default:
					MandaRespuesta("FindHome", "ERR_NA");
					ledRojo.Pulsos(1500,500,3);
					break;
					break;
			}

		break;

	default:
		MandaRespuesta("FindHome", "ERR_NA");
		ledRojo.Pulsos(1500,500,3);
		break;
	}

}
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
void loop() {
	
}

#pragma endregion


/// FIN DEL PROGRAMA ///

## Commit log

2019-01-28 Agregar archivos de proyecto.
2019-01-28 Actualizado a Framework 4.5.2 para compatibilidad con libreria MQTT
2019-01-31 Iniciado Codigo de Arduino para ESP-12E
2019-02-04 Incluido codigo Arduino para control Shutter
2019-02-05 Doc de comunicaciones
    [Comunicaciones.ods]
2019-02-05 MQTT Arduino
2019-02-07 HW Azimut base de comunicaciones OK
    [Comunicaciones.ods]
2019-02-07 Determinar una version unica para el CAD ( Freecad )
2019-02-11 Añadidos comandos via Serie para configuracion de Wifi y MQTT
2019-02-11 Mejorada la gestion de la WIFI. Añadido gestion por linea de comandos via puerto serie. Comando WIFI. Añadidos comandos via Serie para gestion de la conexion MQTT
2019-02-20 Actualizacion documentacion comunicaciones
    [Comunicaciones.ods]
2019-02-21 Ordenar el codigo. Comunicaciones OK. Gestion de LWT OK y probada. Comandos via Serie. Actualizacion de DOC
    [Comunicaciones.ods]
2019-02-21 Currelo a saco
    [Comunicaciones.ods]
2019-02-22 Trabajando en el Objeto Cupula en Arduino
2019-02-26 Currando con el objeto BMDome1
2019-02-28 Implementando clase BMDomo1
    [Comunicaciones.ods]
2019-03-01 Trabajando en la clase BMDomo1
    [Comunicaciones.ods]
2019-03-07 Mas currelo. Afinando el MoveTo y añadido algun comando mas.
    [Comunicaciones.ods]
2019-03-09 Funcion GOTO
    [Calculadora.ods]
2019-03-20 Funcion GOTO OK
    [Calculadora.ods]
2019-03-22 Adaptando a ESP32 y libreria WiFiMQTTManager
2019-03-25 Borrar lo de Visual Studio
2019-03-25 Proyecto migrado a ESP32 y Visual Code Platform IO
2019-03-25 Adaptando a ESP32 y Platform.IO
2019-03-29 Ajustando el lio MQTT (Strings y c_str)
2019-04-01 Ajuste de Tareas
2019-04-09 Tareas. Problemas de InstrFetchProhibited
    [main.cpp]
2019-04-12 Mejorando control Stepper
2019-04-15 Core1 para Stepper
2019-04-17 Actualizacion Motores
2019-04-17 Golpe motor casi quitado del todo
2019-04-23 Versión del código de Azimut al que le he añadido la parte del shutter (compuerta)
2019-04-25 Caja Electrica 1
    [Cuadro_electrico_1.FCStd]
2019-05-15 Pre Adaptar Lib Stepper
2019-05-23 Libreria Accelstepper ESP32 Timer
2019-05-27 Motor OK
2019-05-27 Implementando Comandos
    [Comunicaciones_Azimut.ods, Comunicaciones_plantilla.ods]
2019-05-29 Mas Comandos
    [Comunicaciones_Azimut.ods]
2019-06-25 Reloj NTP y config de sensores para HomeAssistant
2019-07-08 DXF Files
    [Lateral_Base_Motor.dxf, Soporte_rodillos_V01.dxf]
2019-10-22 CAD Version 3
    [6310-2Z.FCStd, 8mm Bearing SKF 608 RS 286-7530.STEP, AnguloFijacion.FCStd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]
2019-10-23 Actualizacion CAD
    [Cremallera.FCStd, Soporte_rodillos_V01 (2).FCStd, Tapa_Rodamiento.FCStd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]
2019-10-23 DXF varios
    [#Angulo_Fijacion_taladros_cara1.dxf, #Base_Motor.dxf, Angulo_Fijacion_taladros_cara1.dxf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]
2019-10-28 3 tornillos mas en lateral base motor
    [AnguloFijacion.FCStd, Angulo_Fijacion.dxf, Angulo_Fijacion_Taladros_1.dxf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]
2022-04-21 Placa Azimut
    [PlacaIOAzimut-B_CrtYd.gbr, PlacaIOAzimut-B_Cu.gbr, PlacaIOAzimut-B_Fab.gbr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]
2022-05-20 CAD Placa, fabricacion PCBWay
    [Angulo_Fijacion.CATPart, Angulo_Fijacion.step, Base_Motor.CATPart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]
2022-07-30 Tapa Rodamiento V2
    [Tapa_Rodamiento_V2-Body.step, Tapa_Rodamiento_V2.FCStd]
2022-07-30 Tapa Rodamiento V2 CAM
    [Tapa_Rodamiento_V2-Body.CATPart, Tapa_Rodamiento_V2.dxf]
2022-07-30 Tapa rodamiento cam fresa 4mm
